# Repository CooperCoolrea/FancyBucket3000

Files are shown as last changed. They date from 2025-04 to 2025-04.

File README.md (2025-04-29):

# FancyBucket3000

## Summary of Project
The Fancy Bucket 3000 is a rain collection system with volume sensing, pH sensing, and an automatic valve opening for irrigation systems. This system utilizes an ultrasonic sensor to determine when the rain barrel is getting full and will notify the user that water testing needs to be done before releasing the water to the plants. We integrated a digital pH sensor to report the acidity of the water to the user and recommend treatments if necessary. There is also manual pH entry if the user prefers to use pH strips. Once the user has treated the water, they can push a button on our UI to open a ball valve to release the water to the irrigation system. This system will consist of piping from the Fancy Bucket 3000 to a prepared trough with soil and plants. Our project is fully operational and meets all outputs listed in the project initiation.

## Design Description
### Materials

**Table 1: Bill of Materials**

| **Part Number** | **Part Name** | **Description** | **Notes** | **Quantity** | **Units** | **Total Cost** | **Supplier** | **Supplier Part Number** | **Link** | **Package Size** | **Unit** | **Package price** |
|---|---|---|---|---|---|---|---|---|---|---|---|---|
| 1001 | Plastic Bucket | 5-Gallon, HDPE | Comes with wire handle | 1.0 | each | 3.73 | Menards | 6482910 | [Link](https://www.menards.com/main/grocery-home/cleaners-household-essentials/cleaning-supplies/cleaning-tools/menards-reg-5-gallon-bucket/6482910/p-1444426310607-c-7113.h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) | 1.0 | each | 3.73 |
| 1002 | pH sensor | Teyleten pH detection sensor | arduino compatible | 1.0 | each | 18.99 | Amazon | B09H1MJS4S | [Link](https://www.amazon.com/dp/B09H1MJS4S) | 1.0 | each | 18.99 |
| 1003 | Wood Glue | Gorilla Wood Glue |  | 0.12 | fl oz. | 0.1191 | Home Depot | 62020 | [Link](https://www.homedepot.com/p/Gorilla-4-oz-Wood-Glue-62020/100672057) | 4.0 | fl oz. | 3.97 |
| 1004 | Ball Valve | U.S. Solid Motorized Ball Valve- 1/2" Brass Ball Valve | 9-24V AC/DC and 2 Wire Auto Return Setup | 1.0 | Each | 34.02 | Amazon | ANSI B16.34, IP65 | [Link](https://www.amazon.com/dp/B072QW8ST4) | 1.0 | Each | 34.02 |
| 1005 | 1 inch Plywood | 3/4 inch thick, sanded plywood |  | 225.0 | Sq in | 4.666 | Home Depot | 205960 | [Link](https://www.homedepot.com/p/Handprint-3-4-in-x-2-ft-x-4-ft-Sanded-Plywood-205960/205960) | 1152.0 | Sq in | 23.89 |
| 1006 | Porch screening | Charcoal fiberglass screen roll |  | 33.18 | sq in | 0.262 | Home Depot | FCS10396-M | [Link](https://www.homedepot.com/p/Saint-Gobain-ADFORS-36-in-x-84-in-Charcoal-Fiberglass-Screen-Roll-FCS10396-M/203176333) | 3024.0 | sq in | 11.48 |
| 1007 | 2.5 inch screws | Coarse zinc-plated steel square-head pocket screw |  | 16.0 | each | 2.71 | Home Depot | SML-C250-50 | [Link](https://www.homedepot.com/p/Kreg-2-1-2-in-Coarse-Zinc-Plated-Steel-Pocket-Screws-50-Pack-SML-C250-50/100401223) | 50.0 | each | 8.47 |
| 1008 | 1.25 inch screws | Square maxi-Loc head coarse zinc-plated steel pocket-hole screw |  | 12.0 | each | 1.14 | Home Depot | SML-C125-100 | [Link](https://www.homedepot.com/p/Kreg-1-1-4-in-Square-Maxi-Loc-Coarse-Zinc-Plated-Steel-Pocket-Hole-Screw-100-Pack-SML-C125-100/100401222) | 100.0 | each | 9.47 |
| 1009 | Epoxy | Gorilla Clear Epoxy Adhesive | 2 part epoxy | 0.85 | fl oz. | 7.48 | Lowes | 13111000 | [Link](https://www.lowes.com/pd/Gorilla-Epoxy-Clear-Epoxy-Adhesive/5002785627) | 0.85 | fl oz. | 7.48 |
| 1010 | Bucket lid | Standard lid for 5 gallon plastic pail |  | 1.0 | each | 2.00 | Uline | S-9948BLU | [Link](https://www.uline.com/Product/Detail/S-9948BLU/Pails/Standard-Lid-for-35-5-6-and-7-Gallon-Plastic-Pail-Blue) | 1.0 | each | 2.00 |
| 1011 | Bucket connector | 1/2 in. PVC schedule 40 male adapter |  | 1.0 | each | 0.59 | Home Depot | PVC021090600HD | [Link](https://www.homedepot.com/p/Charlotte-Pipe-1-2-in-PVC-Schedule-40-Male-MPT-x-S-Adapter-PVC021090600HD/203811636) | 1.0 | each | 0.59 |
| 1012 | Silicone caulk | GE Silicone 1 All Purpose Clear Caulk |  | 1.5 | oz | 1.32 | Lowes | 2795576 | [Link](https://www.lowes.com/pd/GE-Silicone-1-All-Purpose-Windows-Doors-Exteriors-10-1-oz-Clear-Silicone-Caulk/5013443639) | 10.1 | oz | 8.88 |
| 1013 | 0.25 inch Plywood | 1/4 in. x 2 ft. x 2 ft. Sanded Plywood Project Panel |  | 38.5 | sq in. | 0.53 | Home Depot | 300810 | [Link](https://www.homedepot.com/p/Handprint-1-4-in-x-2-ft-x-2-ft-Sanded-Plywood-Project-Panel-) | 576 | sq in. | 7.88 |

### Drawings and Circuit Diagrams

<p align="center">
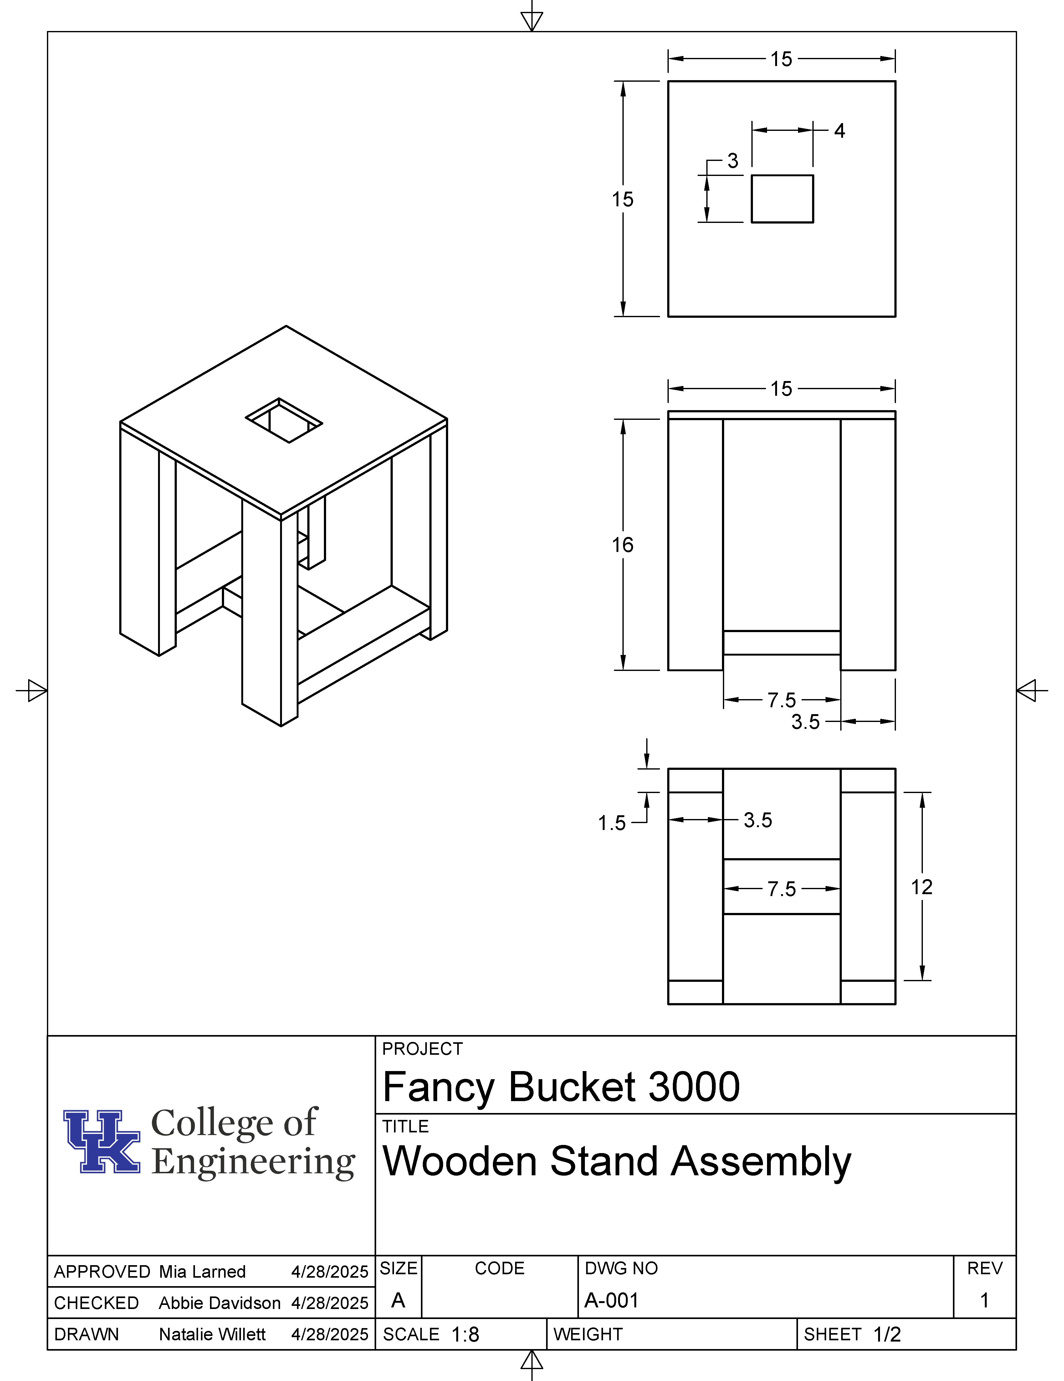
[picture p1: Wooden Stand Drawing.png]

</p>
<p align="center">
  <em>Figure 1: 3D model of wooden stand</em>
</p>

<p align="center">
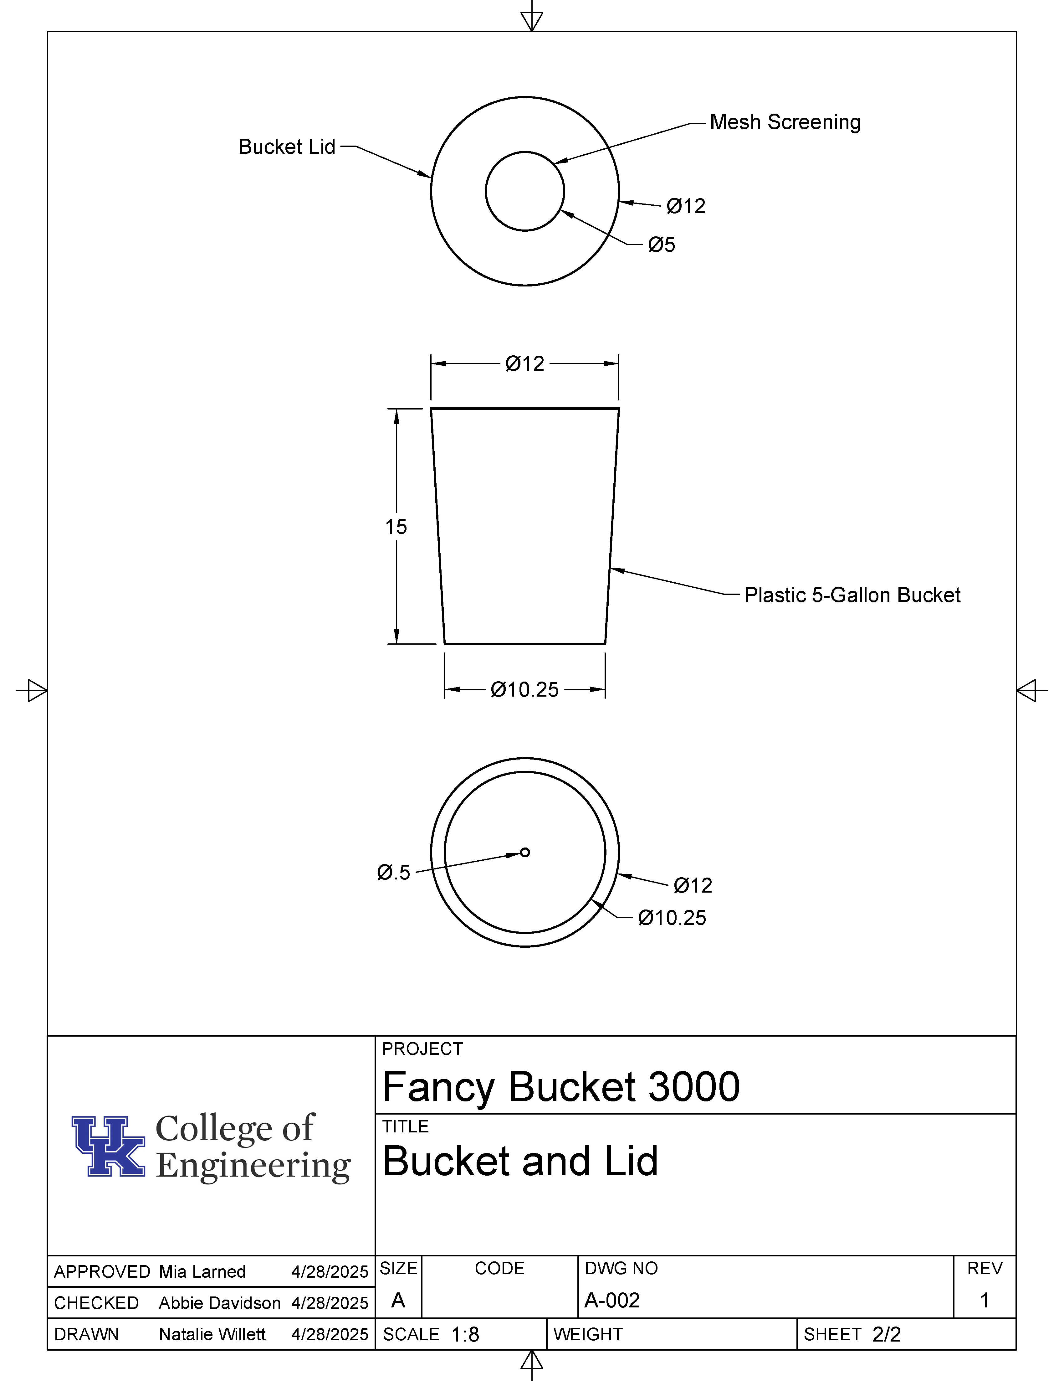
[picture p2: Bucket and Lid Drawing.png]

</p>
<p align="center">
  <em>Figure 2: 3D Model of Bucket and Lid Design</em>
</p>

<p align="center">
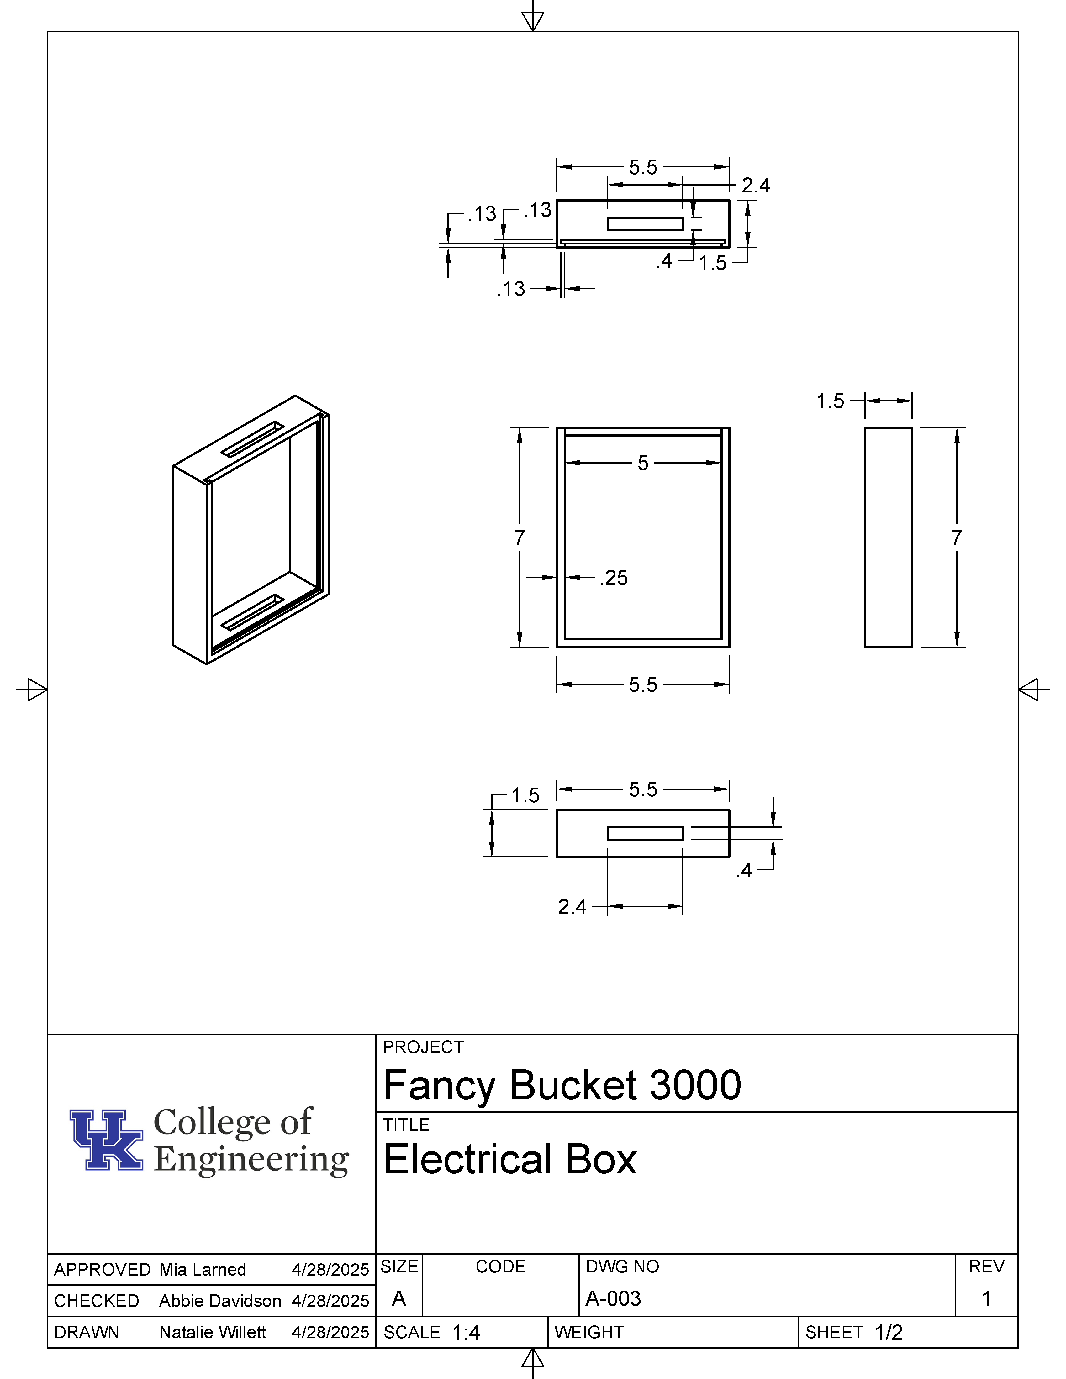
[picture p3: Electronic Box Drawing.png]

</p>
<p align="center">
  <em>Figure 3: 3D Model of Waterproof Box</em>
</p>

<p align="center">
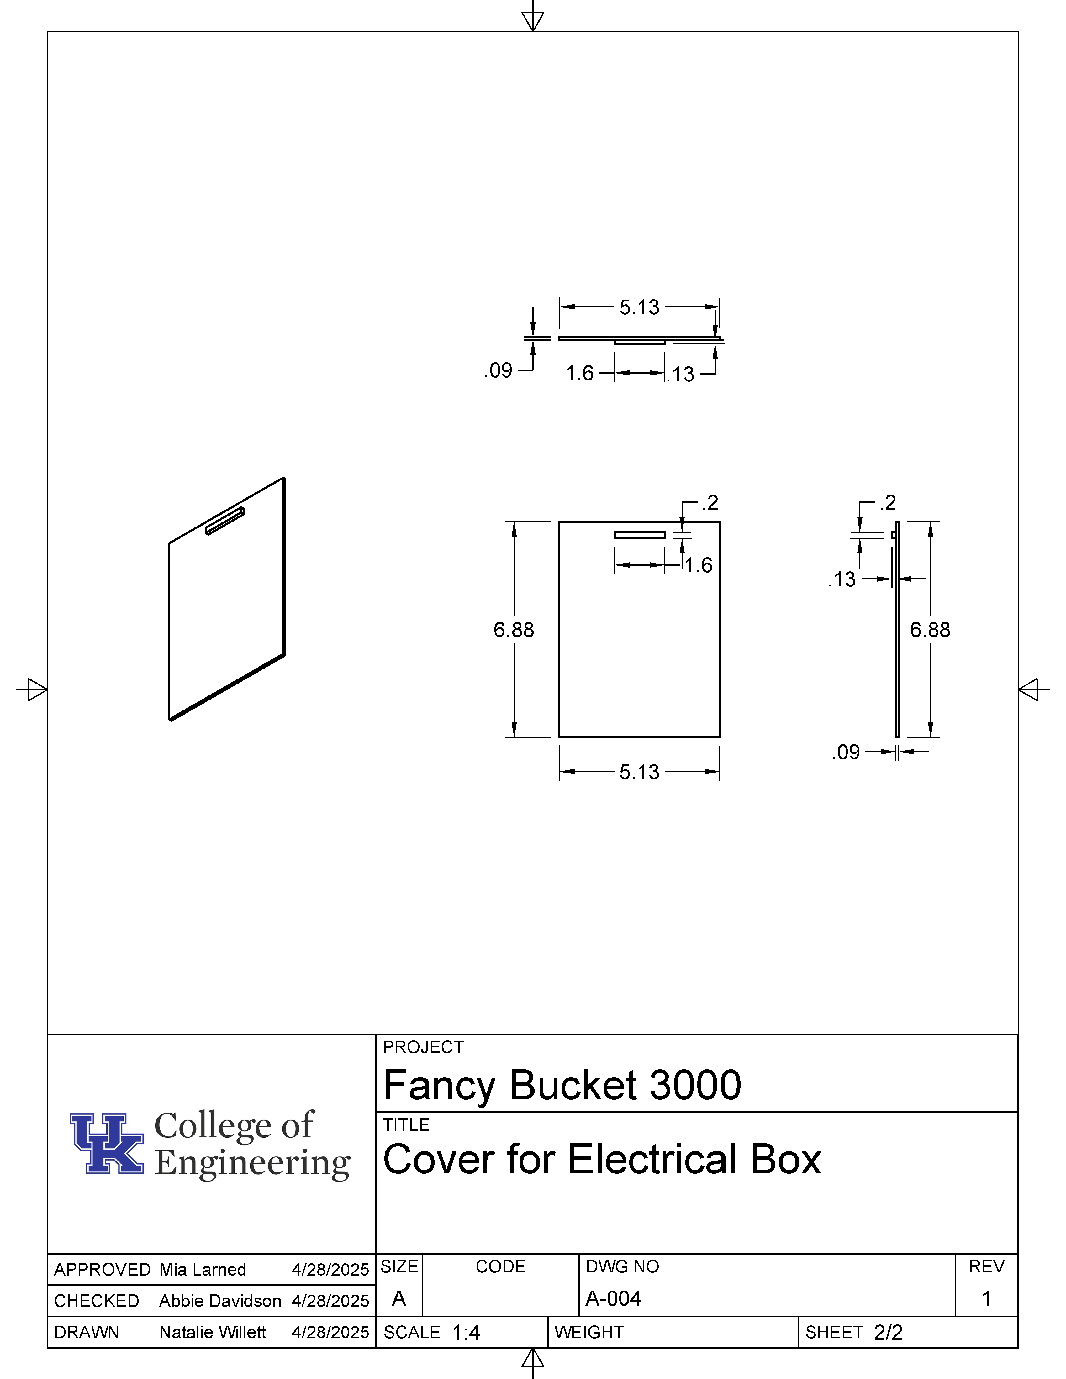
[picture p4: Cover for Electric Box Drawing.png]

</p>
<p align="center">
  <em>Figure 4: 3D Model of Waterproof Box Lid</em>
</p>

<p align="center">
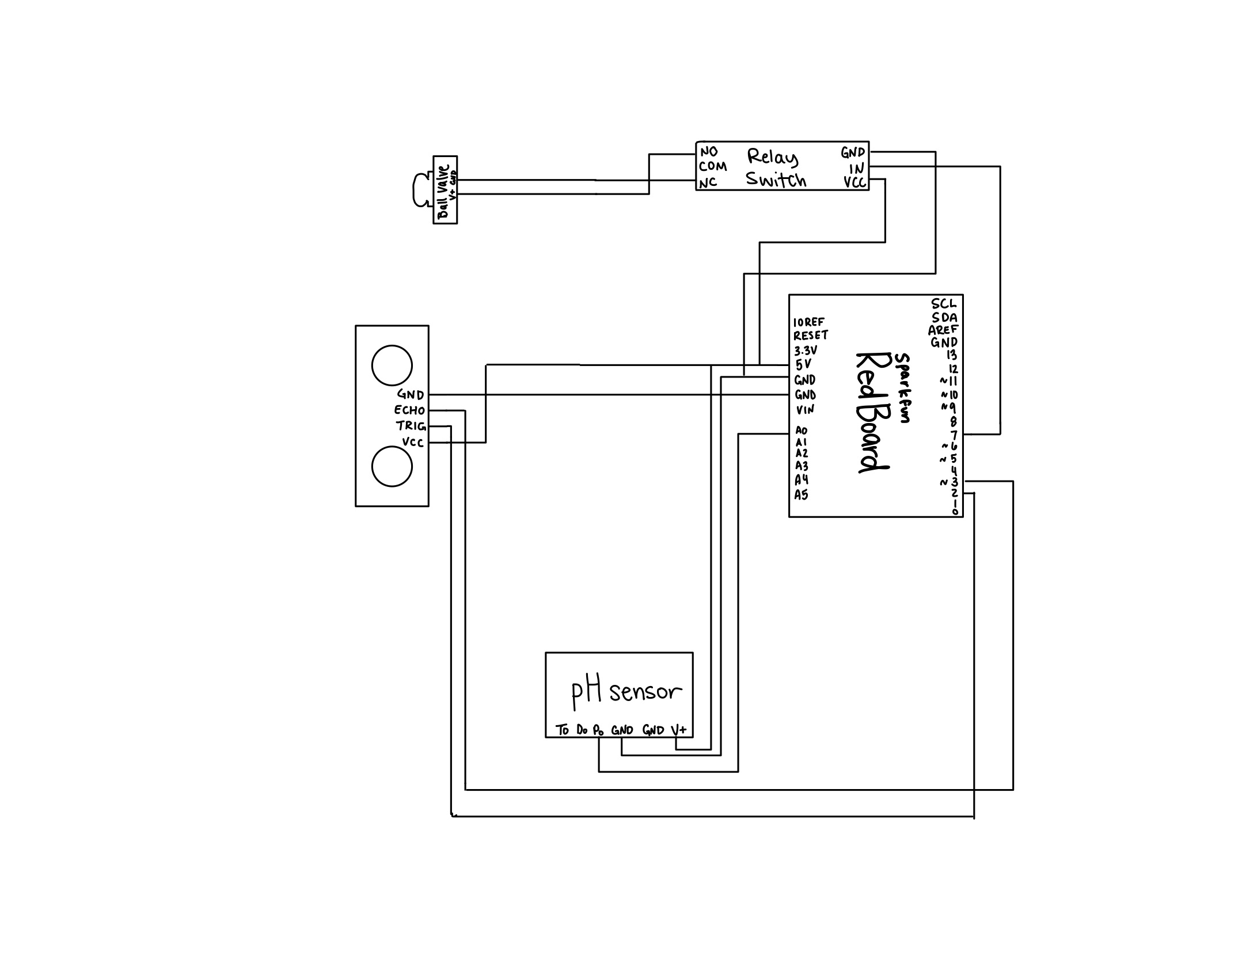
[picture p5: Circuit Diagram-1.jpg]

</p>
<p align="center">
  <em>Figure 5: Circuit Drawing</em>
</p>

### Code

The following code was used to control the components attached to our RedBoard.
```cpp
// Valve control pins
const int VALVE_ON = 7;

// Ultrasonic sensor pins
const int TRIG_PIN = 2;
const int ECHO_PIN = 3;

// pH sensor pin
const int PH_PIN = A0;

// Bucket dimensions (in inches)
const float BUCKET_HEIGHT_IN = 15.0;
const float DIAMETER_TOP = 12.0;
const float DIAMETER_BOTTOM = 10.25;

String inputCommand = "";
bool showCloseMessage = false;
unsigned long closeMessageStart = 0;
unsigned long lastVolumePrintTime = 0;

bool valveOpen = false;
bool manualOverride = false;

void setup() {
  pinMode(VALVE_ON, OUTPUT);
  digitalWrite(VALVE_ON, LOW);

  pinMode(TRIG_PIN, OUTPUT);
  pinMode(ECHO_PIN, INPUT);

  Serial.begin(9600);
  Serial.println("System ready. Type 'open', 'close', or 'ph'.");
}

void loop() {
  float distance_cm = readDistanceCM();
  float gallons = calculateGallons(distance_cm);

  // Display gallons every 2 seconds
  if (millis() - lastVolumePrintTime >= 2000) {
    Serial.print("Water Level: ");
    Serial.print(gallons, 2);
    Serial.println(" gallons");
    lastVolumePrintTime = millis();
  }

  // Auto control only if no manual override
  if (!manualOverride) {
    if (!valveOpen && distance_cm < 10.0) {
      Serial.println("Fancy Bucket 3000 too full. Releasing some water");
      digitalWrite(VALVE_ON, HIGH);
      valveOpen = true;
    } 
    else if (valveOpen && distance_cm >= 12.0) {
      digitalWrite(VALVE_ON, LOW);
      valveOpen = false;
      Serial.println("Sufficient water released.");
    }
  }

  // Handle serial input
  if (Serial.available() > 0) {
    inputCommand = Serial.readStringUntil('\n');
    inputCommand.trim();

    if (inputCommand == "open") {
      Serial.println("Manual override: opening valve.");
      manualOverride = true;
      digitalWrite(VALVE_ON, HIGH);
      valveOpen = true;
    }

    else if (inputCommand == "close") {
      Serial.println("Manual override: closing valve.");
      manualOverride = false;
      digitalWrite(VALVE_ON, LOW);
      valveOpen = false;
      showCloseMessage = true;
      closeMessageStart = millis();
    }

    else if (inputCommand == "ph") {
      Serial.println("Have you inserted the pH sensor and begun stirring? (yes/no)");
      while (Serial.available() == 0);
      String confirmation = Serial.readStringUntil('\n');
      confirmation.trim();

      if (confirmation == "no") {
        Serial.println("Please insert the pH sensor and gently stir with it, then type 'ph' again when ready.");
      }
      else if (confirmation == "yes") {
        Serial.println("Continue gently stirring for 5 seconds...");
        for (int i = 5; i > 0; i--) {
          Serial.print(i);
          Serial.println("...");
          delay(1000);
        }

        float pH = readPH();
        Serial.print("pH: ");
        Serial.println(pH, 2);

        if (pH >= 6.5 && pH <= 8.5) {
          Serial.println("pH is safe! Water is suitable for release.");
        }
        else if (pH < 6.5) {
          Serial.println("Your water is currently acidic. To make your water safe to release, please use baking soda to raise the pH.");
        }
        else {
          Serial.println("Your water is currently basic. To make your water safe to release, please use diluted white vinegar to lower the pH.");
        }
      }
    }
  }

  if (showCloseMessage && millis() - closeMessageStart >= 4000) {
    Serial.println("Valve closed. Power off.");
    showCloseMessage = false;
  }
}

// Sensor functions

float readDistanceCM() {
  digitalWrite(TRIG_PIN, LOW);
  delayMicroseconds(2);
  digitalWrite(TRIG_PIN, HIGH);
  delayMicroseconds(10);
  digitalWrite(TRIG_PIN, LOW);

  long duration = pulseIn(ECHO_PIN, HIGH);
  return duration * 0.0343 / 2.0;
}

float calculateGallons(float distance_cm) {
  float distance_in = distance_cm / 2.54;
  float water_height = BUCKET_HEIGHT_IN - distance_in;
  if (water_height <= 0) return 0.0;

  float r1 = DIAMETER_BOTTOM / 2.0;
  float r2 = DIAMETER_TOP / 2.0;

  float volume_cubic_in = (1.0 / 3.0) * PI * water_height * (r1 * r1 + r1 * r2 + r2 * r2);
  return (volume_cubic_in / 231.0) - 1;
}

float readPH() {
  int adc = analogRead(PH_PIN);
  float voltage = adc * (5.0 / 1023.0);
  float pH = -5.70 * voltage + 29.18;
  return pH;
}
```

The following code created our user interface on streamlit.
```cpp
import tkinter as tk
from tkinter import messagebox
# from PIL import Image, ImageTk
import serial
import threading
import time

# ----- Serial Setup -----
SERIAL_PORT = 'COM5'  # Adjust to match your system
BAUD_RATE = 9600
ser = serial.Serial(SERIAL_PORT, BAUD_RATE, timeout=1)

# ----- GUI Setup -----
root = tk.Tk()
root.title("💧 Fancy Bucket 3000")
root.configure(bg="#1e1e1e")

# ----- Rain Drop Icon (optional) -----
try:
    rain_img = Image.open("rain_drop.png").resize((40, 40))
    rain_icon = ImageTk.PhotoImage(rain_img)
    left_rain = tk.Label(root, image=rain_icon, bg="#1e1e1e")
    left_rain.grid(row=0, column=0, padx=(10, 5), pady=10)
    right_rain = tk.Label(root, image=rain_icon, bg="#1e1e1e")
    right_rain.grid(row=0, column=3, padx=(5, 10), pady=10)
except:
    left_rain = tk.Label(root, text="💧", font=("Arial", 24), fg="white", bg="#1e1e1e")
    left_rain.grid(row=0, column=0, padx=(10, 5), pady=10)
    right_rain = tk.Label(root, text="💧", font=("Arial", 24), fg="white", bg="#1e1e1e")
    right_rain.grid(row=0, column=3, padx=(5, 10), pady=10)

# ----- Water Level Label -----
water_label = tk.Label(root, text="Water Level: -- gallons", font=("Arial", 18), fg="white", bg="#1e1e1e")
water_label.grid(row=0, column=1, columnspan=2, pady=10)

# ----- pH Status Label -----
ph_status = tk.Label(root, text="Prompting pH sensor...", font=("Arial", 12), fg="gray", bg="#1e1e1e")
ph_status.grid(row=1, column=0, columnspan=4, pady=4)

# ----- Command Buttons -----
def send_command(cmd):
    ser.write((cmd + "\n").encode())

def open_valve():
    ph_status.config(text="Opening valve...", fg="white")
    send_command("open")
    root.after(4000, lambda: ph_status.config(text="Valve opened.", fg="green"))

def close_valve():
    ph_status.config(text="Closing valve...", fg="white")
    send_command("close")
    root.after(4000, lambda: ph_status.config(text="Valve closed.", fg="green"))

def check_ph():
    send_command("ph")
    ph_status.config(text="Prompting pH sensor...", fg="white")
    yes_button.grid(row=3, column=1)
    no_button.grid(row=3, column=2)

def manual_ph():
    ph_status.config(text="Select the measured pH range:", fg="white")
    low_button.grid(row=4, column=0, pady=4)
    mid_button.grid(row=4, column=1, pady=4)
    high_button.grid(row=4, column=2, pady=4)

def handle_manual_ph(level):
    low_button.grid_remove()
    mid_button.grid_remove()
    high_button.grid_remove()
    if level == "low":
        messagebox.showinfo("Recommendation", "Your water is currently acidic. Please use baking soda to raise the pH.")
    elif level == "mid":
        messagebox.showinfo("Recommendation", "pH is safe! Water is suitable for release.")
    elif level == "high":
        messagebox.showinfo("Recommendation", "Your water is currently basic. Please use diluted white vinegar to lower the pH.")

def handle_yes():
    send_command("yes")
    yes_button.grid_remove()
    no_button.grid_remove()

def handle_no():
    send_command("no")
    yes_button.grid_remove()
    no_button.grid_remove()

open_button = tk.Button(root, text="Open Valve", width=12, command=open_valve)
open_button.grid(row=2, column=0, pady=10)

close_button = tk.Button(root, text="Close Valve", width=12, command=close_valve)
close_button.grid(row=2, column=1, pady=10)

check_button = tk.Button(root, text="Use pH Sensor", width=16, command=check_ph)
check_button.grid(row=2, column=2, pady=10)

manual_button = tk.Button(root, text="Manual pH Entry", width=16, command=manual_ph)
manual_button.grid(row=2, column=3, pady=10)

# ----- pH Response Buttons -----
yes_button = tk.Button(root, text="Yes", command=handle_yes)
no_button = tk.Button(root, text="No", command=handle_no)

low_button = tk.Button(root, text="pH < 6.5", command=lambda: handle_manual_ph("low"))
mid_button = tk.Button(root, text="6.5 ≤ pH ≤ 8.5", command=lambda: handle_manual_ph("mid"))
high_button = tk.Button(root, text="pH > 8.5", command=lambda: handle_manual_ph("high"))

# ----- Serial Reading Thread -----
def read_serial():
    while True:
        if ser.in_waiting:
            line = ser.readline().decode(errors="ignore").strip()
            if "Water Level" in line:
                try:
                    value = line.split(":")[-1].strip()
                    water_label.config(text=f"💧 Water Level:{value} gallons")
                except:
                    pass
            elif "please use" in line.lower() or "pH is safe" in line:
                messagebox.showinfo("pH Recommendation", line)
            elif "please insert" in line.lower():
                ph_status.config(text=line, fg="yellow")
            elif "stirring" in line.lower():
                ph_status.config(text=line, fg="white")
            elif "Have you inserted" in line:
                ph_status.config(text=line, fg="white")
                yes_button.grid(row=3, column=1)
                no_button.grid(row=3, column=2)
            else:
                ph_status.config(text=line, fg="white")
        time.sleep(0.5)

thread = threading.Thread(target=read_serial, daemon=True)
thread.start()

# ----- Run GUI -----
root.mainloop()
```

### Assembly Instructions
**Bucket and Stand Assembly**
1. To assemble the bucket and stand, we started by using a compass to outline the size of the hole we wanted to cut in the lid. Using a drill, we made a hole inside of the circle we drew to make a starting point to cut the circle out. Using a jig saw, we cut the circle out of the lid.

2. We cut a circle out of the screening that was slightly bigger than the hole cut in the lid. Using a scrap piece of cardboard as a mixing plate and a paint stick we mixed the gorilla two part epoxy. We used the paint stick to dab the epoxy on the perimeter of the circle, and placed the cut screening on the epoxy. We tapped the screen down onto the epoxy while wearing gloves, then taped the sides of the screen down to dry, as shown in the image below.
<p align="center">
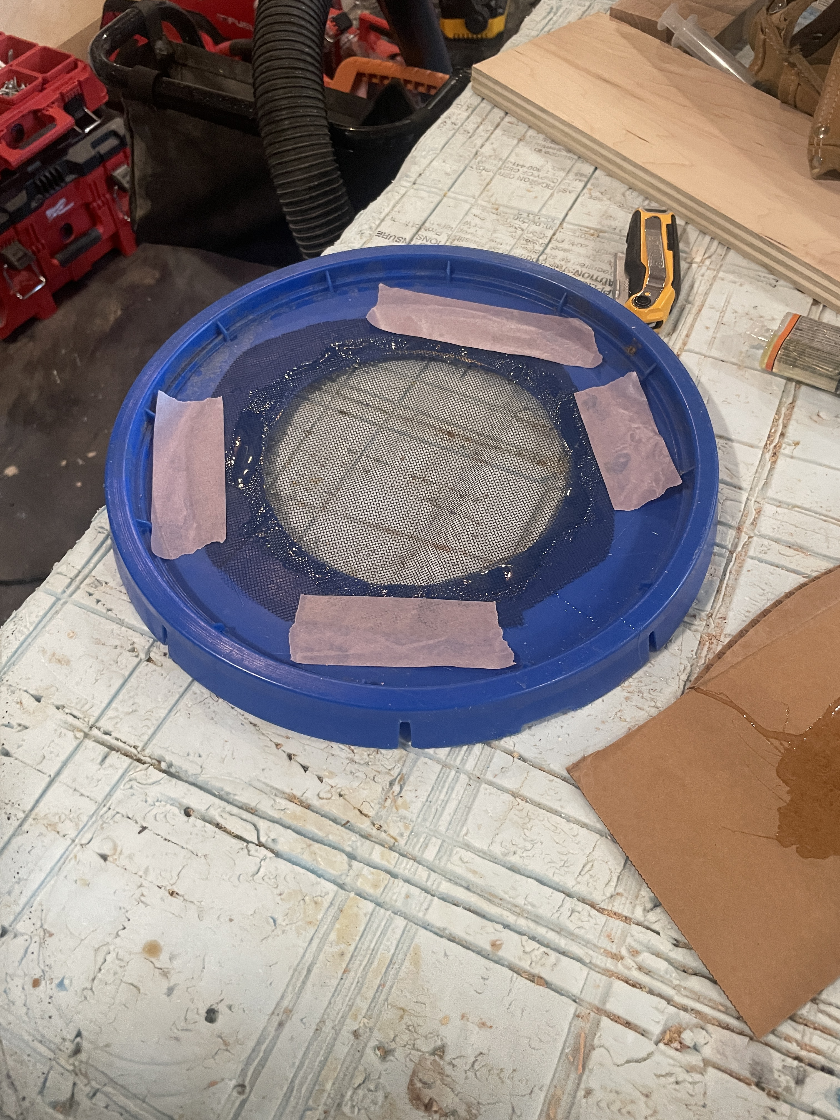
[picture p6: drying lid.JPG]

</p>
<p align="center">
  <em>Figure 6: Lid and Mesh Cover Drying After Assembly</em>
</p>

3. Using a table saw, we cut a 16" by 16" square. Using a Miter Saw, we cut 4 16" long pieces, two 12" long pieces, and one 8" long piece from the 2-in x 4-in lumber. 

4. Starting with the 16" long pieces, we calibrated our pocket hole guide and drilled 3 pocket holes on one side of the pieces. The same thing was done on the 12" long pieces, and 8" piece, but 6 holes total were cut. Three holes in a row, but done on both sides of the same surface.

5. Once all pocket holes were drilled, we spread wood glue on the cut edge of the 16" pieces, on side with the pocket holes. The glue was placed down on the corner of the plywood piece, and a clamp was used to secure it in place. Using XXX inch screws, we drilled the screws into the pocket holes to fully secure the legs of the stand. 

6. The same process was done with the 12" long pieces, but they were clamped horizontally between the legs, 1 inch down from the base of the legs. For the 8" piece, it was glued horizontally between the two 12" pieces. All of these pieces were clamped down and set to dry overnight. The following image shows the pieces together, clamped down to dry. 
<p align="center">

</p>
<p align="center">
  <em>Figure 7: Wooden Stand Drying After Assembly</em>
</p>

7. For the valve portion of the bucket, we used a drill with a step cone drill bit attachment to make a 1/2 inch hole in the center of the bottom of the bucket. We applied silicone caulk  to the area around the hole on the inside of the bucket, and screwed in the pipe attachment as far as it could go. This was left to dry overnight. When the bucket was eventually dry, a wrench was used to hold the pipe in place while the sensor was glued on. 
 
8. To cut the hole in the wooden stand, we sketched out an area around the size of the entire valve, and used an oscillating saw to cut out the hole. 

9. For the waterproof box around our electronics, we 3D modeled and printed a box and sliding door in Autodesk Fusion. The following image shows the printed electronic box and cover, and the 3D model is shown in the Drawings section.

<p align="center">
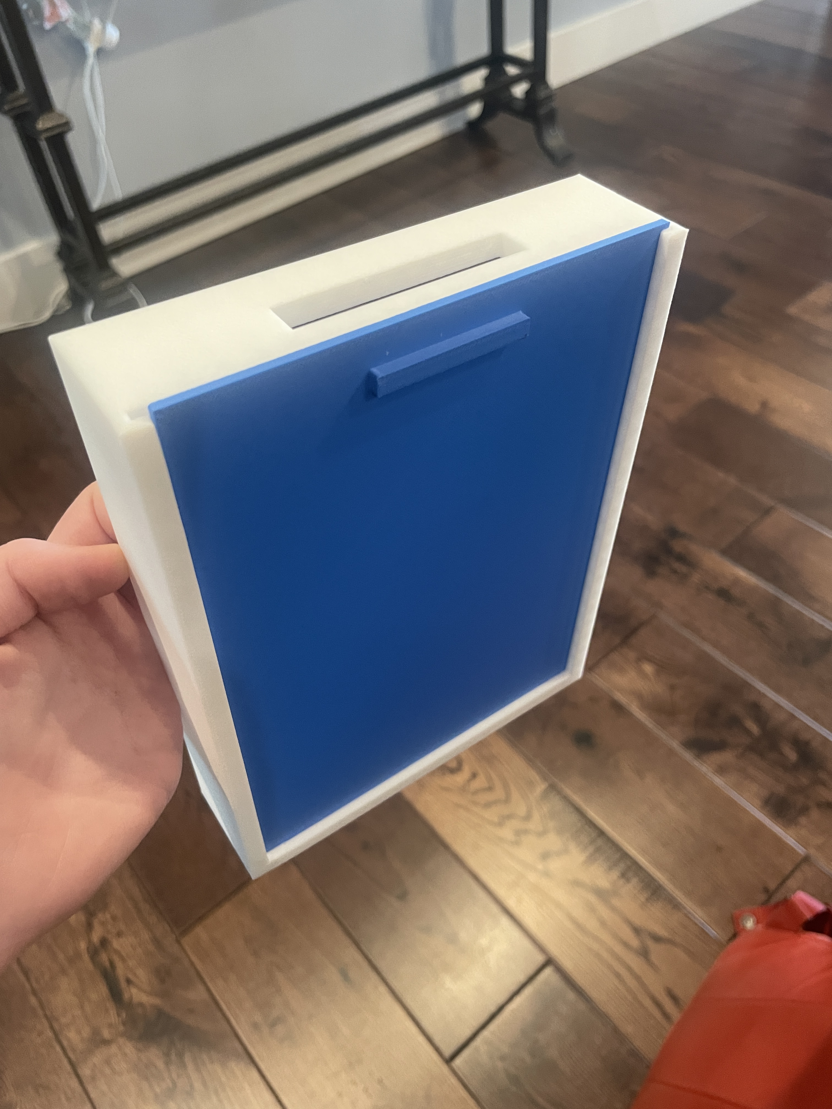
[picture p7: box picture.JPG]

</p>
<p align="center">
  <em>Figure 8: Final 3D Printed Box and Lid</em>
</p>

10. When the box was printed, we had to drill some holes in the box to allow for wires to get out, these are shown below. We held our circuit up to the box, and sketched out where we needed the holes, then drilled them around 1/4 to 1/2 inch in diameter. 

<p align="center">
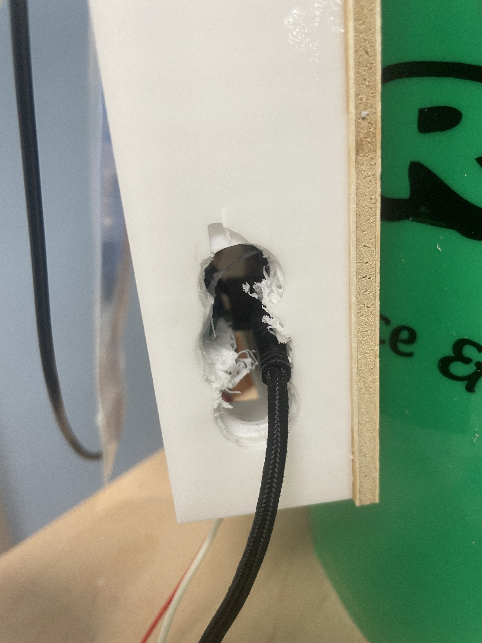
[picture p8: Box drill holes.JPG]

</p>
<p align="center">
  <em>Figure 9: Electronic Box Drill Holes</em>
</p>

11. For the electronics box, we needed to add a piece of plywood to the back to make it able to be attached. We cut a piece of 1/4 inch plywood that was the same size as the outer edge of the box shown in the drawings section (7 inch by 5.5 inch), then used small amounts of epoxy on the corners of the box to hold it together. We taped the box and wood together on every side, then left it to dry overnight. When the epoxy was dry, we peeled off the tape. 

12. To attach the ultrasonic sensor to the bucket, we used the same step cone drill bit attachment to make a small hole one inch down from the top of the bucket. Then, we taped the ultrasonic sensor with the wires attached to it in the hole, making sure the sensor was angled to be perpendicular to the bottom of the bucket so we could get the best reading. We also put tape on the sensors themselves to make sure no caulk would obstruct them. This was then caulked in place, and left to dry overnight. The tape placement and caulk are shown in the images below. Once the caulk was dry, we peeled off the tape.

<p align="center">
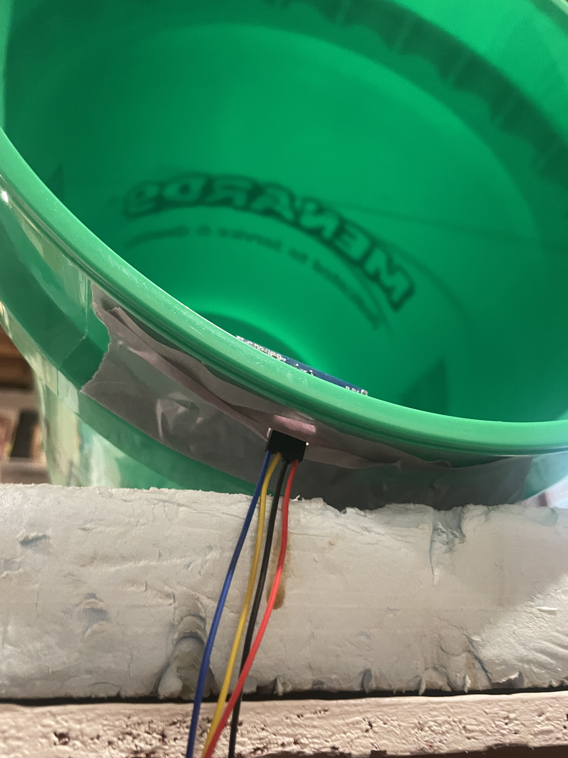
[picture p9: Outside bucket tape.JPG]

</p>
<p align="center">
  <em>Figure 10: Tape on the Outside of the Bucket</em>
</p>

<p align="center">
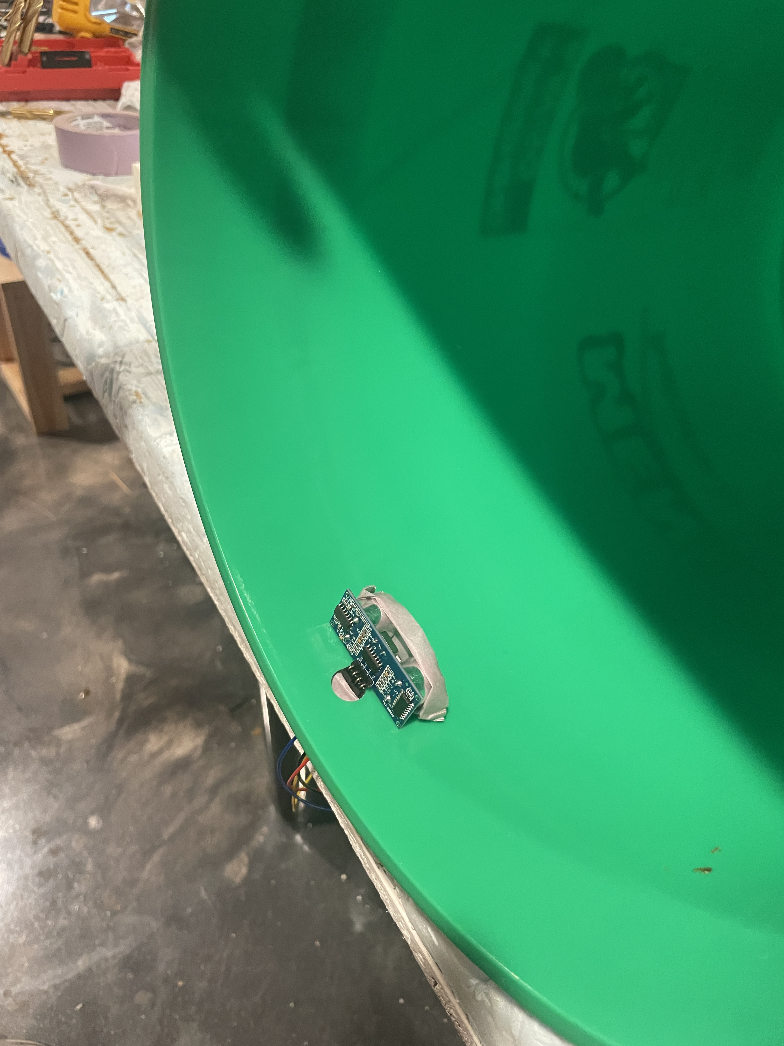
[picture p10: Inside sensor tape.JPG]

</p>
<p align="center">
  <em>Figure 11: Tape on the Sensor Inside the Bucket</em>
</p>

<p align="center">
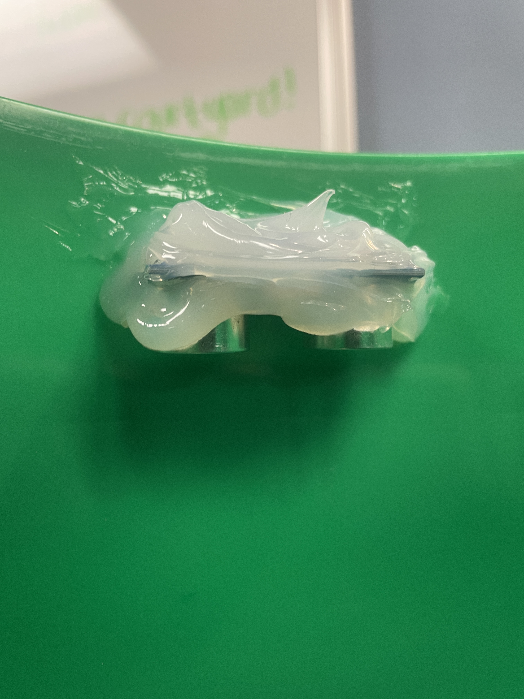
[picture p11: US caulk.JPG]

</p>
<p align="center">
  <em>Figure 12: Final Sensor with Caulk</em>
</p>

13. To attach the electronics box, we put a vertical line of the same caulk down the center of back of the plywood attached to the box. We laid the box face down on a table, then placed the side of the bucket on top of it, positioning the box to be approximately 3 inches below the hole we cut for the ultrasonic sensor. The bucket was propped up in position by objects we had, then left to dry overnight.

14. We used some double sided tape to hold the circuit in place when we open and close the electronics box, and threaded all of the appropriate wires through. After this, the Fancy Bucket 3000 was fully assembled!

<p align="center">

</p>
<p align="center">
  <em>Figure 13: Final Fancy Bucket 3000</em>
</p>

**Circuit**
1. To construct our system, we first built a simple circuit that included a ball valve and a motor controller.
2. Next, we had to create a second power supply for the ball valve. One thing that we did not originally consider when we ordered the ball valve was that it required at least 9 Volts of power to function properly. Our Redboard could only provide 5 Volts and the battery pack that came with our Sparkfun Inventor Kit could only provide 6 Volts (1.5 Volts per battery). Thus, we found a 12 Volt source, then retrofit the wires to fit the ground and positive wires of the connector of the double A battery pack holder. After stripping the wires, we used a multimeter to determine which wire was positive and which was negative. Then, we soldered them to the battery pack connecter and wrapped the wires in electrical tape.
3. Next, we added a pH sensor. We connected wires to the ports on the pH sensor for power, ground, and one labled "Po" to represent pH output.
4. Finally, we incorporated an ultrasonic sensor. The final circuit diagram can be seen in figure 14. A picture of our final circuit can be seen in figure 15.

<p align="center">

</p>
<p align="center">
  <em>Figure 14: Circuit Diagram </em>
</p>

<p align="center">
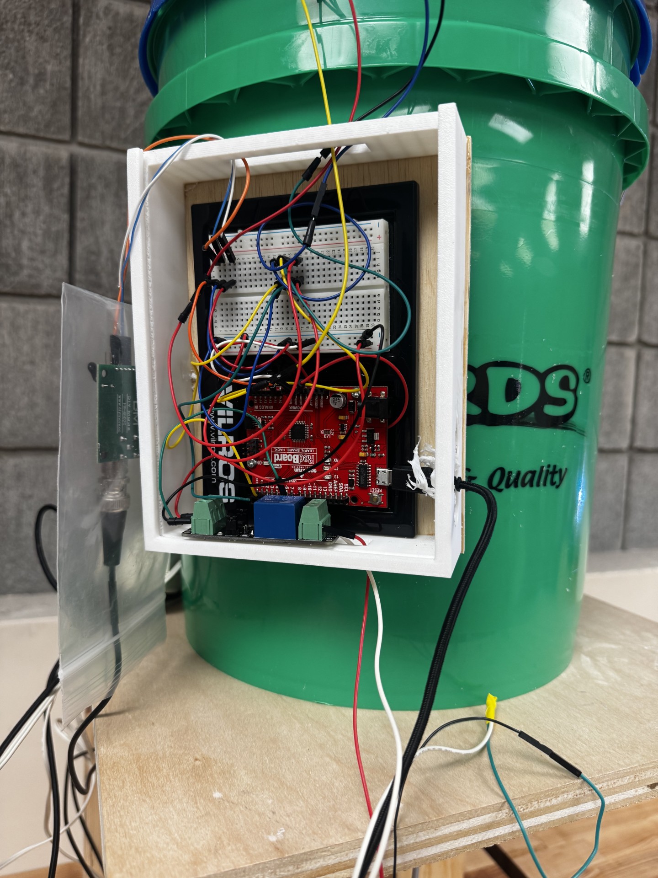
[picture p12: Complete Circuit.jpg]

</p>
<p align="center">
  <em>Figure 15: Completed Circuit </em>
</p>

**Software and GUI**
1. To create the code for our project, we prompted ChatGPT to create a script for Arduino IDE that controls an electronic ball valve, a pH sensor, and an ultrasonic sensor. To control the electronic ball valve, the program needed to open the valve with the click of a button and automatically close the valve after water has been released. The pH sensor needed to read the pH accurately, report it to the user, and provide a treatment recommendation. The ultrasonic sensor needed to report the volume to the user and notify the user when it is too full.
2. After ChatGPT provided the code, we tested it with our circuit design. If it did not work appropriately, we would identify the issue, then prompt ChatGPT to fix it. We continued this process until our code worked successfully.
3. Once we had a working code, we had ChatGPT rewrite it in Python to be used in Visual Studio with a user interface (UI).

## Testing Description
### Test Equipment
* Cups of water from different sources

### Testing Procedures
Could another test engineer replicate your tests?
All test equipment specified (model numbers) and procedures fully described

**Volume Sensing**
1. To test if the ultrasonic sensor was working correctly and that our GUI was showing the correct volume, we would first fill our bucket to any depth.
2. Then, we would measure the depth and multiply that depth by the cross sectional area of the bucket. 
3. Finally, we would run our code and see if the volume value it was reporting was approximately the same as the calculated value. If it was not, we would recallibrate our code and rerun the test.

**pH Sensing**
1. To test the pH sensor, we filled cups with fluids that had different pH values. 
2. Then we would remove the pH sensor from its cover and insert it into the different fluids.
3. Between each different solution, we made sure to insert the probe into distilled water as a calibration technique.
4. Finally, we would ensure that the pH values being reported by the serial monitor were approximately correct by seeing if the reported value was in the estimated range the fluid should be in. If we were testing the pH sensor in an extremely acidic solution like vinegar, we knew our pH sensor was not working if it was reporting a neutral pH around 7.
5. Initially, our pH sensor was reporting very similar, neutral values no matter what fluid it was submerged in. To fix this, we integrated a calibration function into our code. Based on the voltage the probe was measuring in distilled water, the calibration function ensured that the output would be close to a neutral pH of 7. Once we utilized the calibration function, we recieved accurate pH results in different solutions.

**Automatic Ball Valve**
1. To test the automatic valve opening, we merely had to run our code and click the button on our GUI that was labeled “Open Valve.” If the valve opened, we considered that to be a successful trial.
2. Then, to test the closing function, we clicked the button on our GUI that was labeled “Close Valve.” If the valve closed, that was a successful trial. 
3. Finally, the valve needed to close automatically when it was empty. To test this, we would allow the bucket to release all of its contents, then we would observe the behavior of the ball valve. If it closed after releasing all the water, we considered that a successful trial.

## Design Decision Discussion
One of the first design decisions we made was to put a lid on our bucket with a large hole cutout with a mesh covering. This prevents leaves from getting in the bucket and allows water to enter. The border of the cutout is where the ultrasonic sensor rests. This prevents it from being rained on from above; however, the sensor would still be at risk of water damage if the bucket overfills. There is definitely room to improve this design. For example, someone could add a cover that automatically closes the bucket when it gets full. This would eliminate any risk of water damage. Additionally, there is some interference with the ultrasonic sensor's sound pulses bouncing off the bucket lid. This created some inaccurate volume results.

Another design decision we made was to use a ball valve as the connection between the water storage and water distribution. We mainly decided to use a ball valve because we were afraid that a solenoid valve would be unable to open with the amount of pressure at the bottom of our bucket. Additionally, a ball valve only requires a switch to operate, while a solenoid requires some analog signals to control it. We also considered rigging up an automatic opening with a servo or stepper motor; however, we decided that neither motor would have the power to open against the pressure of the water. The ball valve we used was also fairly simple to implement after having a proper power supply. We merely had to connect it to a motor controller and code it like any other component. Using a servo, stepper motor, or solenoid valve would've required more work and troubleshooting.

We decided to use an electronic pH sensor in the interest of time. It was very simple to code and calibrate. We also included a manual option on our GUI in case our users wanted to use a paper pH strip, then input their own reading. We were originally going to use a camera and code it to read the pH from the color; however, we decided this would be difficult since we would have to worry about interference from background colors and potentially would’ve had to utilize artificial intelligence. We also considered only using a manual option; however, we wanted to challenge ourselves and did not want there to have to be a secondary purchase to use our device. Another engineer could implement the camera reading with artificial intelligence or use manual entry only for simplicity.

We decided to 3D print a plastic box to hold our Redboard and circuitry because we wanted to protect the electronics from water damage. The lid of our electronic box includes a holder for the pH sensor. It may have been simpler to cut out a box from wood or metal; however, we did not want to have to wait for glue to dry, weld, or seal the box. Additionally, other engineers could improve on our design by making the box more flush with the curved surface of the bucket. We made ours flat and caulked it, because it was quick and effective. We also kept in mind that this was just a prototype.

One design challenge we debated at the beginning stages of our project was where to put the outlet of our bucket. We were debating whether or not to put it on the bottom surface or whether to put it on the side of the bucket. We decided to put it on the bottom since it allowed for minimal water stagnation, it provided clearance for our hose, and we had gravity working to encourage flow downward. One issue with this location is that our internal pipe connection is not entirely flush with the bottom and extends upward into the bucket. This means the bucket will never be completely empty. Another engineer could improve our design by slanting the inside of the bottom of the bucket. This would prevent any stagnation.

## Test Results Discussion
**Volume Sensing**

The volume sensing function exhibited consistent but slightly elevated baseline readings when water was input. Across trials with different numbers of gallons of water added, the sensor detected a small offset ranging from 0.21 to 0.29 gallons. Although the sensor did not register a perfect value, the measurements were relatively stable and within a narrow range, suggesting good repeatability. The consistent offset indicates that while the sensor is reliable in detecting changes in volume, it may have a systematic calibration error that causes a slight overestimation at very low volumes. This behavior would have minimal impact during normal operation, where larger volume changes are of primary concern.

**pH Sensing**

In testing the pH sensor, we first calibrated it using distilled water to ensure it returned accurate baseline readings, which it did relatively reliably, yielding a constant pH value of 6.45. We deemed this accurate, as the pH of distilled water in Lexington is around 5.8. However, when we tested the sensor with other common solutions such as water mixed with vinegar (acidic) and water mixed with baking soda (basic), the sensor displayed little to no variation in the pH readings. Despite the expected chemical changes, the sensor readings remained largely unchanged, indicating a malfunction. To confirm that the issue was with the probe itself and not our system design, we tested another group’s pH sensor with our setup, and it responded accurately to the solutions. This verified that the problem was isolated to our pH probe. Based on these observations, we concluded that our original pH probe was defective. To address this issue and maintain functionality, we integrated a manual pH input option into our GUI. This allows users to enter accurate pH values themselves, ensuring that the system can still provide appropriate treatment suggestions based on reliable input.

**Automated Ball Valve**

The automatic valve responded reliably to user input provided through our GUI application. Specifically, each time the user clicked the designated button on the app interface, the valve successfully opened as intended. During all five experimental trials, the valve consistently released the water contained in the bucket immediately following the user’s command. Similarly, each time the user pressed the button to close the valve, it closed successfully during all five trials. This consistent performance across multiple repetitions demonstrates that the system's valve control functionality operated with perfect precision, achieving a 100% success rate for both opening and closing operations. The seamless interaction between the software interface and the hardware mechanism confirms that the valve accurately and promptly executed the user’s instructions without any delay or malfunction, highlighting the reliability and effectiveness of our system's automated water release feature.

The ball valve demonstrated excellent accuracy in responding to the barrel reaching maximum capacity. In all five trials, the detected volume exceeded the required threshold of 3.66 gallons, and the valve opened successfully each time. The measured volumes ranged from 3.69 to 4.48 gallons, consistently surpassing the minimum capacity requirement. Additionally, after the water level dropped below the threshold, the valve reliably closed in each case, further confirming the system’s responsiveness and control. This consistent behavior highlights the valve's strong performance and reliability in both preventing overfilling and maintaining proper barrel management.

## Testing Results

**Volume Sensing**

**Table 1: Accuracy of Volume Sensing Function**
|Trial|Measured Volume of Water Inputted (gal)|Volume Detected (gal)|
|---|---|---|
|1|0|0.22|
|2|1|1.23|
|3|2|2.29|
|4|2.5|2.71|
|5|3|3.22|

**pH Sensing**

**Table 2: Accuracy of pH Sensing Function**
|Trial|Solution|Anticipated pH|pH Detected|
|---|---|---|---|
|1|Distilled Water|~5.8|6.45|
|2|Distilled Water|~5.8|6.45|
|3|Distilled Water|~5.8|6.45|
|4|Vinegar and Water Solution|~4-5 (Acidic)|6.47|
|5|Baking Soda and Water Solution|~8-9 (Basic)|6.53|

**Automated Ball Valve**

**Table 3: Accuracy of Valve Opening Prompted by User**
|Trial|Button Clicked (Yes/No)|Valve Open? (Yes/No)|
|---|---|---|
|1 |Yes|Yes|
|2 |Yes|Yes|
|3 |Yes|Yes|
|4 |Yes|Yes|
|5 |Yes|Yes|

**Table 4: Accuracy of Valve Closing Prompted by User**
|Trial|Button Clicked (Yes/No)|Valve Close? (Yes/No)|
|---|---|---|
|1 |Yes|Yes|
|2 |Yes|Yes|
|3 |Yes|Yes|
|4 |Yes|Yes|
|5 |Yes|Yes|

**Table 5: Accuracy of Valve Opening Prompted by Capacity of Barrel**
|Trial|Volume Detected (gal)|Required Volume for Maximum Capacity(gal)|Valve Open? (Yes/No)|
|---|---|---|---|
|1 |4.46| &ge;3.66 |Yes|
|2 |4.42| &ge;3.66|Yes|
|3 |4.48| &ge;3.66|Yes|
|4 |3.69| &ge;3.66|Yes|
|5 |4.18| &ge;3.66|Yes|

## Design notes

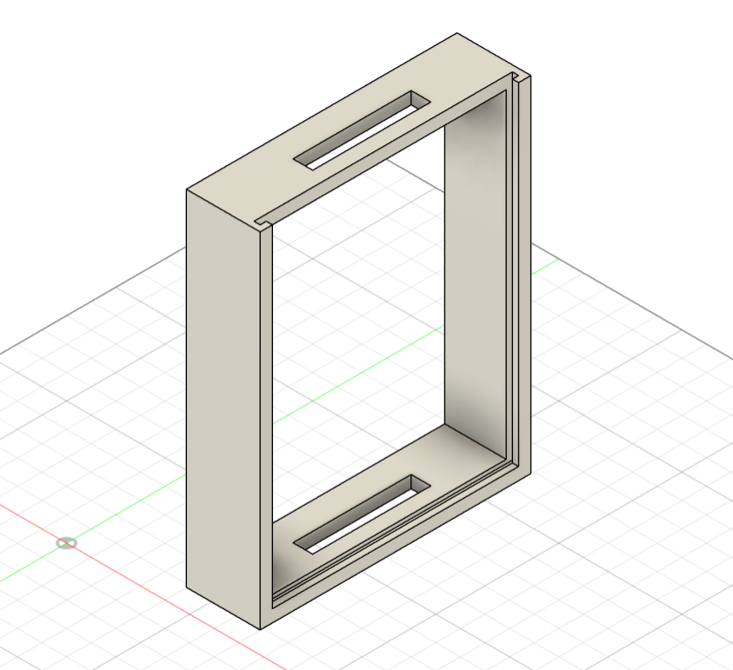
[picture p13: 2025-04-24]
3D box.png

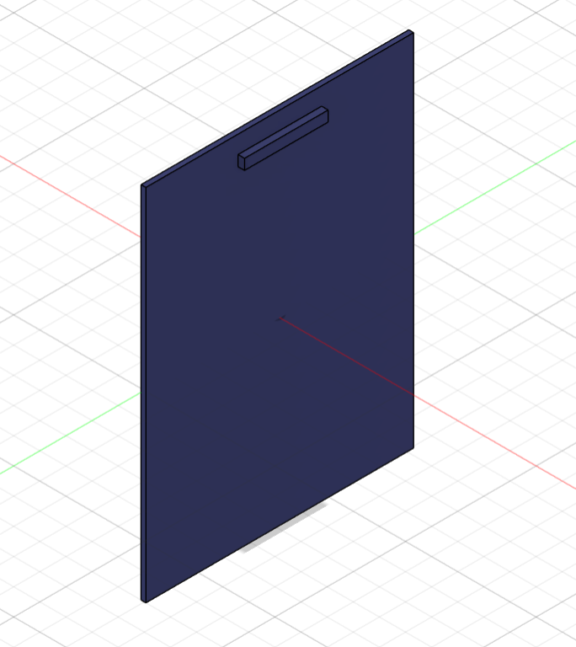
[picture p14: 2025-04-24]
3D lid.png

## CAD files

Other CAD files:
Fancy Bucket 3000.f3d

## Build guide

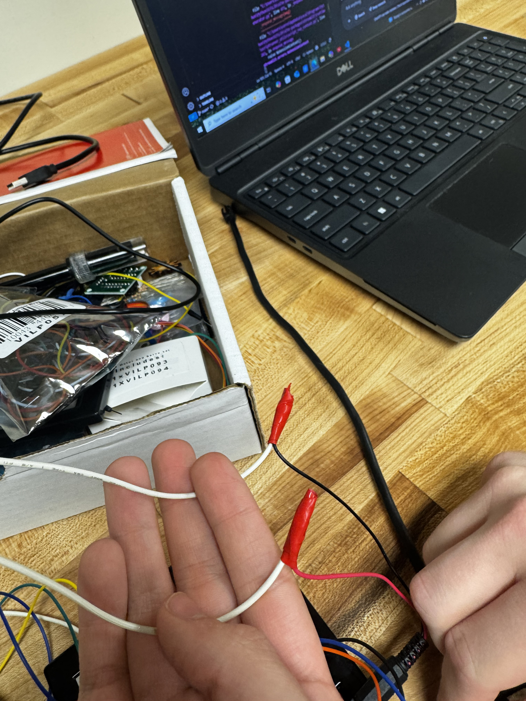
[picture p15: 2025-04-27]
Soldered-Wires.jpg

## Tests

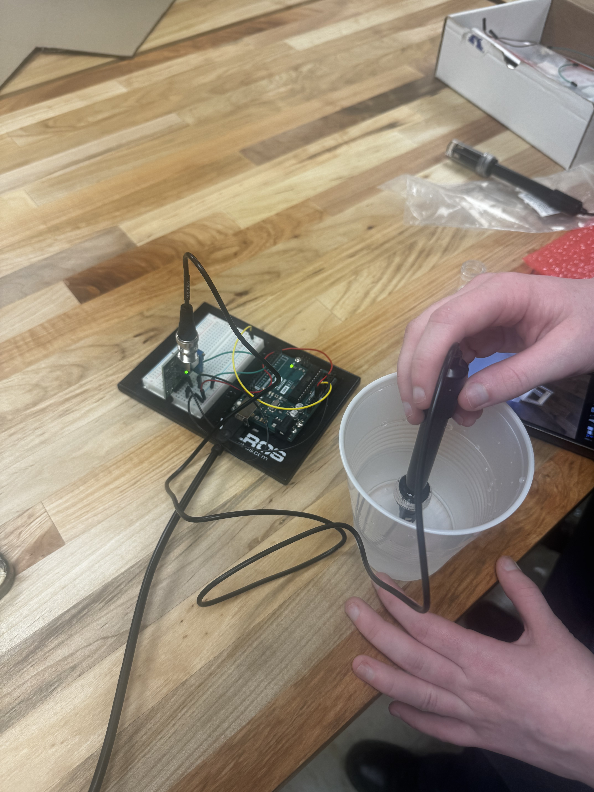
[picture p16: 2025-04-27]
pH-testing.jpg

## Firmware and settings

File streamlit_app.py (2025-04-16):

import streamlit as st
import serial
import time

# Set up serial connection (adjust port & baudrate if needed)
SERIAL_PORT = 'COM3'  # Replace with your actual COM port (e.g. 'COM4' or '/dev/ttyUSB0')
BAUD_RATE = 9600

# Try to establish the serial connection once
@st.cache_resource
def get_serial_connection():
    return serial.Serial(SERIAL_PORT, BAUD_RATE, timeout=2)

ser = get_serial_connection()

st.title("Valve Controller")

# Button for Open
if st.button("Open Valve"):
    ser.write(b"open\n")
    st.write("Opening valve...")
    time.sleep(4)
    st.write("Valve opened. Power on.")

# Button for Close
if st.button("Close Valve"):
    ser.write(b"close\n")
    st.write("Closing valve...")
    time.sleep(4)
    st.write("Valve closed. Power off.")

# Button for Distance
if st.button("Get Distance"):
    ser.write(b"distance\n")
    time.sleep(0.5)
    output = ser.readline().decode().strip()
    if "Distance:" in output:
        st.success(output)
    else:
        st.warning("No distance response received.")

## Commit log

2025-04-24 Circuit Diagram
2025-04-29 Rename Circuit Diagram-1.jpg to Old Circuit Diagram-1.jpg
2025-04-29 Rename Circuit Diagram-1 (1).jpg to Circuit Diagram-1.jpg
2025-04-29 Rename Circuit Diagram-1.jpg to Old Circuit Diagram-2.jpg
